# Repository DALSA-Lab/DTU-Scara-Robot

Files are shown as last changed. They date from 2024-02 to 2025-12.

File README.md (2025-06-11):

# Bioscara - DALSA DIY SCARA robot arm
This repository serves to collect all information regarding DTU DALSAs DIY robot arm Bioscara version 2.
Version 2 is defined by replacing the MKS SERVO42C stepper drivers with the Ustepper S32 drivers and removing the 3D printer board. The orignal repository can be found in the bioscara_v1 branch.

## Documentation
The documentation for the joint communication interface can be found in [/docs](/docs/). The documentation is made with Doxygen, its configuration file is in the root of the folder. The documentation can be found as a pdf [/docs/latex/refman.pdf](/docs/latex/refman.pdf) and as html in [/docs/html/index.html](/docs/html/index.html)

## Usage
The robots controller is a Raspberry Pi 4. The RPI is configured to connect to a WIFI network with the the following credentials:  
**SSID**: DALSA_IOT  
**Password**: dalsa_iot  
The easiest way to establish the network is to create a WIFI hotspot with the above credentials, however static IP assignemnt is not possible using Windows Hotspot, and hence the IP address must be checked before any connection attempt.
On the RPI remote login and remote desktop as well as SSH is activated. This way the desktop can be accessed through a RDP software like Windows Remote Desktop or Remina. Be carefull that connecting this way will create a new user session!

Interacting with the robot is handled through ROS2. In the subdirectory a seperate README can be found explaining how to use the hardware.

## TODO
### Mechanical
- [ ]  Update the Fusion model to with all new parts.
- [x] combine old and new stp and stl files
- [ ] Fix J3 Pulley slipping by increasing surface roughness
- [ ] Gripper Redesign
### Software
- [ ] Finish the TODO list for the Joint Communication Protocol (see the documentation)
- [ ] Create URDF file
- [ ] Get started with MoveIt
### Documentation
- [ ] Continue this TODO list and Readme
- [ ] Improve User guide with detailed descriptions and up to date 3D models
- [ ] Document mechanical changes
- [ ] Document Ubuntu install and configurations
- [ ] Document ROS installation
- [ ] Explain the scripts

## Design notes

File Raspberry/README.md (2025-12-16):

# Setup on the Raspberry Pi
> [!CAUTION]
>
> This list is under development and not complete (yet)

- Install Ubuntu Server 24.04 LTS
- Install openssh-server
- Run the scripts provided in [/scripts](scripts)

## Creating the boot image
Using the latest version of the [Raspberry Pi imager](https://www.raspberrypi.com/software/), flash an SD card (16GB, Class 10) with Ubuntu 24.04 LTS Server.
> [!IMPORTANT]
>
> Since the HDMI ports of the Raspberry Pi are no longer accessible when installed inside the robot, follow the next steps to configure remote access.
> Otherwise you would not even be able to see the shell of the OS.

Flash the SD card with the boot image, you dont need to set custom settings, this will be done in the next step.

When the flashing is finished, copy the [*network-config*](network-config) and [*user-data*](user-data) files to the boot/ partition of the SC card. The *network config* contains the initial netplan configuration. Setting the renderer to NetworkManager sets the WiFi managed by the NetworkManager and hence tools like the nmcli can be used. This file will only be read once per instance (during the first boot). The contents of *network-config* will be copied to */etc/netplan/50-cloud-init.yaml* [Link](https://docs.cloud-init.io/en/latest/reference/network-config-format-v2.html#netplan-passthrough).

The netplan contains the following configutation:
- Sets the Netplan renderer (the backend for which Netplan is creating the configuration files) to NetworkManager.
  - **NOTE**: For unknown reasons while testing theses instructions it has happened that the Pi was not connecting to the AP nor ethernet (and the credentials were 100%). Logging into the Pi with a screen attached showed that the NetworkManager was not installed on the system, this should not happen on a clean installation. If that should happed try one of the following:
    - Create a new boot SD card, but edit *network-config* to use 'networkd' (the systemd-networkd network service) instead of 'NetworkManager' as the Netplan rendered. The when booted up and connected to a network install the NetworkManager (`sudo apt install network-manager`). Edit */etc/netplan/50-cloud-init.yaml* back to 'NetworkManager' as renderer and apply `sudo netplan apply`. The network should now be up and managed by the NetworkManager, not systemd-networkd.
    - Instead of creating a new boot image, connect to the Pi's shell by attaching display and keyboard and change the renderer to 'networkd', apply 'sudo netplan apply', wait for connection `sudo netplan status -a`, then continue as described above with downloading the NetworkManager.
- Wifi:
  - Saves an AP with the SSID: 'DALSA_IOT' and pre-shared key: 'dalsa_iot'
  - This AP should be used as a fallback: The raspberry pi will try to connect to this AP if no other is available. You can then gain access to the Pi by creating an AP with the SSID and PSK with a router/laptop hotspot/phone hotspot. All methods should display the IP adrress of the Pi when it is connected.
- Ethernet:
  - Configures static routing for the eth0 interface for a LAN. Refer to the [Network Configuration](#network-configuration) diagram below.
  - The static IP of the robot (the Raspberry Pi) is set to 10.10.10.2.
  - The ethernet route gets assigned a higher metric to route internet traffic through the wifi interface if it is connected, since the LAN has not internet access.

The *user-data* file contains mostly configuration for the user *scara* with the password 'dtubio'. The ubuntu cloud-init program manages these configurations during instance deployment. Many settings can be set here, the README for reference:
>The user-data of the cloud-init seed. This can be used to customize numerous
aspects of the system upon first boot, from the default user, the default
password, whether or not SSH permits password authentication, import of SSH
keys, the keyboard layout, the system hostname, package installation, creation
of arbitrary files, etc. Numerous examples are included (mostly commented) in
the default user-data.
The format of this file is YAML, and is documented at:
https://cloudinit.readthedocs.io/en/latest/topics/modules.html
https://cloudinit.readthedocs.io/en/latest/topics/examples.html

## Network Configuration
The network architecure is as follows:
```mermaid
graph TD;
subgraph Wifi["Wifi"];

laptop["Laptop
hostname: -"]

DTUsecure["DTUsecure

hostname: -"]:::wifi

laptop<-."IP: 10.209.X.X".->DTUsecure

end
subgraph LAN["LAN"];

robot["Raspberry Pi 
hostname: scara"];

dev["Dev Machine
hostname: scara-dev"];

Switch<--IP: 10.10.10.3-->dev
Switch<--IP: 10.10.10.2-->robot

end

Switch<--IP: 10.10.10.4-->laptop
dev<-."(optional)
IP: 10.209.X.X".->DTUsecure
robot<-."(optional)
IP: 10.209.X.X".->DTUsecure
dev<-."(optional)
IP: 10.209.X.X".->laptop
robot<-."(optional)
IP: 192.168.137.X".->laptop

classDef wifi stroke:#f00
classDef bar stroke:#0f0
classDef foobar stroke:#00f
```

The Laptop is optional but usefull during development. In case a Windows hotspot is used the IP addresses are 192.168.137.X (Subnetmask 255.255.255.0).

### Static IP assignment
The */etc/netplan/50-cloud-init.yaml* should have the contents as the [*network-config*](network-config) file, the following snippet configrues the static IP address:
```yaml
...
  ethernets:
    eth0:
      addresses:
        - 10.10.10.2/24
      routes:
        - to: default
          via: 10.10.10.1
          metric: 700 # Increase the metric so that a the wifi connection (metric: 600) is prefered for internet traffic
      nameservers:
          addresses:
            - 8.8.8.8
            - 8.8.4.4
...
```
And the following a simple WPA wifi access point:
```yaml
...
  wifis:
    wlan0:
      dhcp4: true
      optional: true
      access-points:
        "<access-point-SSID>":
          password: "<access-point-psk>"
...
```
to apply changes to Netplan execute:
```bash
sudo netplan apply
```
### Connecting to DTUsecure
If the robot should be connected to DTUsecure, for example for a faster connection, run the provided [script](scripts/connect_DTUsecure.sh). DTUsecure uses the WPA-EAP authethication mechanism with your DTU id and DTU password. The script has been made to simplify the setup.
> [!CAUTION]
>
> Due the nature of the OS, your DTU accounts password will be saved in plain text in a netplan file on the system if the connection shall be saved persistently betweeen reboots! Follow the scripts output to see where.

To run the script first make it executable as follows:
```bash
cd ~/bioscara/Raspberry/scripts
sudo chmod +x connect_DTUsecure.sh
```
then the script can be run simply by invoking:
```bash
sudo ./connect_DTUsecure.sh
```
The script adds a connection via nmcli, and asks the user for DTU id and password and if the credentials should be saved.

### Further information about network management
Managing networks on Linux can be confusing, for example if interfaces show up as 'unmanaged' the chances are high that a different network manager has control over the interface. [This](https://wiki.archlinux.org/title/Network_configuration#Network_managers) table gives a good overview which programs might be involved.
Note that Netplan is not mentioned there, since Netplan only takes a standardized configuration file as input and then depending on the renderer creates the configuration for the backend. Currently Netplan only works with systemd-networkd and NetworkManager, the latter is much simpler to use with its CLI `nmcli`, and terminal UI `nmtui`. 

## Realtime Requirements
Both of the following settings were set to the best realtime performance after the installation of Ubuntu Server 24.04 LTS on the Raspberry Pi. This is how to check and change them if necessary.

This set of kernel configuration is also set when installing the "Low Latency Ubuntu" (`sudo apt install linux-lowlatency`)

### Preemption Policy 

In mainline Ubuntu the maximum preemption policy is PREEMPT. Check if set using:
Check if enabled if CONFIG_PREEMPT is set:
```bash
cat /boot/<BUILD?> | grep CONFIG_PREEMPT
```
last \<BUILD\> = config-6.8.0-1028-raspi

> PREEMPT_VOLUNTARY: This config option adds preemption points to the kernel, enabling voluntary interrupts of low-priority processes. By providing faster application responses with only slightly reduced throughput, CONFIG_PREEMPT_VOLUNTARY suits desktop environments.
>
> PREEMPT: Enabling CONFIG_PREEMPT reduces the kernel latency by making low-priority processes involuntarily preempt themselves. Preemption is disabled only at critical locations where the kernel must protect data from concurrency. Such config option fits embedded applications with latency requirements in the order of milliseconds. [source](https://ubuntu.com/blog/industrial-embedded-systems-ii)

### Interrupt Timer Resolution
> The timer interrupt handler interrupts the kernel at a rate set by the HZ constant. The frequency affects the timer resolutions as a 100 Hz value for the timer granularity will yield a max resolution of 10ms (1 Hz equating to 1000ms), 250Hz will result in 4ms, and 1000Hz in the best-case resolution of 1ms. [source](https://ubuntu.com/blog/industrial-embedded-systems-ii)

```bash
cat /boot/<BUILD?> | grep CONFIG_HZ
```
last \<BUILD\> = config-6.8.0-1028-raspi

### Adding the scara user to realtime group
Add the user to the realtime group and give it the rights to set higher scheduler priotities as described [here](https://control.ros.org/jazzy/doc/ros2_control/controller_manager/doc/userdoc.html#determinism)

| For real-time tasks, a priority range of 0 to 99 is expected, with higher numbers indicating higher priority. By default, users do not have permission to set such high priorities. To give the user such permissions, add a group named realtime and add the user controlling your robot to this group:

```bash
sudo addgroup realtime
sudo usermod -a -G realtime $(whoami)
```
| Afterwards, add the following limits to the realtime group in /etc/security/limits.conf:
```
@realtime soft rtprio 99
@realtime soft priority 99
@realtime soft memlock unlimited
@realtime hard rtprio 99
@realtime hard priority 99
@realtime hard memlock unlimited
```
| The limits will be applied after you log out and in again.

## Other Dependencies
The order of managing dependenices is according to [this](https://ros2-quality-assurance.readthedocs.io/en/released/tutorials/dependencies.html) guideline the following:
1. **rosdep**: Installs missing dependecies specified in the packages via the systems package manager.
2. **vcstool**: Specify further source code repositoryies in a repository file, vcstool will then retrieve the repository and it can then be built with colcon. 
3. **other**

### ROS2 dependencies
To install ROS2 package dependencies navigate to the workspace:
```bash
cd lib/ros2_ws
```

**First:**
Fetch all dependecies that are not available as binaries using the *vcstool*.
From the workspace execute:
```bash
vcs import --recursive src < req.repos
```
This will pull the repositories specified in *req.repos* into the directories also specified in the file.

> [!NOTE]
>
> *vcstool* is found in many ROS2 packages to import dependencies that are not in a ROS or debian repository from a repository file. 
>
> **Installation**:
>
> ```bash
> sudo apt install python3-vcstool
> ```

**Second:**

Install all packages that can be resolved through `rosdep` (all packages that have been released to the ROS2 package ecosystem and some debian packages):
```bash
sudo apt update
rosdep install --from-paths src --ignore-src -y --rosdistro $ROS_DISTRO
```
This command will recursively scan every package in the workspace for the `<depend/>` key and install missing packages.

Then dont forget to build the workspace:
```bash
sudo apt remove ros-$ROS_DISTRO-moveit*
rm -rf build/ install/ log/
MAKEFLAGS="-j1 -l1" colcon build --mixin release --executor sequential --symlink-install > log.out &
```

## Development Purposes:
### Install [PlotJuggler](https://github.com/facontidavide/PlotJuggler)
A very powerfull tool to to display data
```bash
sudo apt install ros-$ROS_DISTRO-plotjuggler-ros
```

### Install RQT tools
```bash
sudo apt install ros-jazzy-rqt*
```

### For debugging
```bash
sudo apt install xterm gdb gdbserver
```

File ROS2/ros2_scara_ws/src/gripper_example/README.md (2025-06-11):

# Robot Gripper  
The gripper is driven by a PWM controlled RC servo. The frequency is 50 Hz. The PWM should be a hardware generated PWM as software PWM has potentiall hight jitter which could cause overheating.
Interacting with the gripper is done through the Gripper class defined in joint_communication/mGripper.h. See the relevant documentation also in the HTML or PDF documentation of the joint_communication protocol.  

## Usage
First build the package with Colcon, then you can run it after it is sourced.
### Building
```bash
cd ~/bioscara/ROS2/ros2_scara_ws
colcon build --packages-select gripper_example
```
### Running
In a new terminal:
```bash
cd ~/bioscara/ROS2/ros2_scara_ws
source install/local_setup.sh
ros2 run gripper_example main 
 ```

Sourcing only is necessary once after opening a new terminal.

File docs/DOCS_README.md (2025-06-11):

# Documentation
This documentation currently documents how the robot controller communicates with the joint controllers, this includes:
- The joint firmware in the [/Arduino](../Arduino/) directory
- The interfacing library used for communicating with the joints in the [/ROS2](../ROS2/ros2_scara_ws/src/joint_communication/) directory.

# Usage
the joint_communication library is structured as a ROS2 package but can also be used in another build toolchain. If that is the case ensure the include paths are still correct.

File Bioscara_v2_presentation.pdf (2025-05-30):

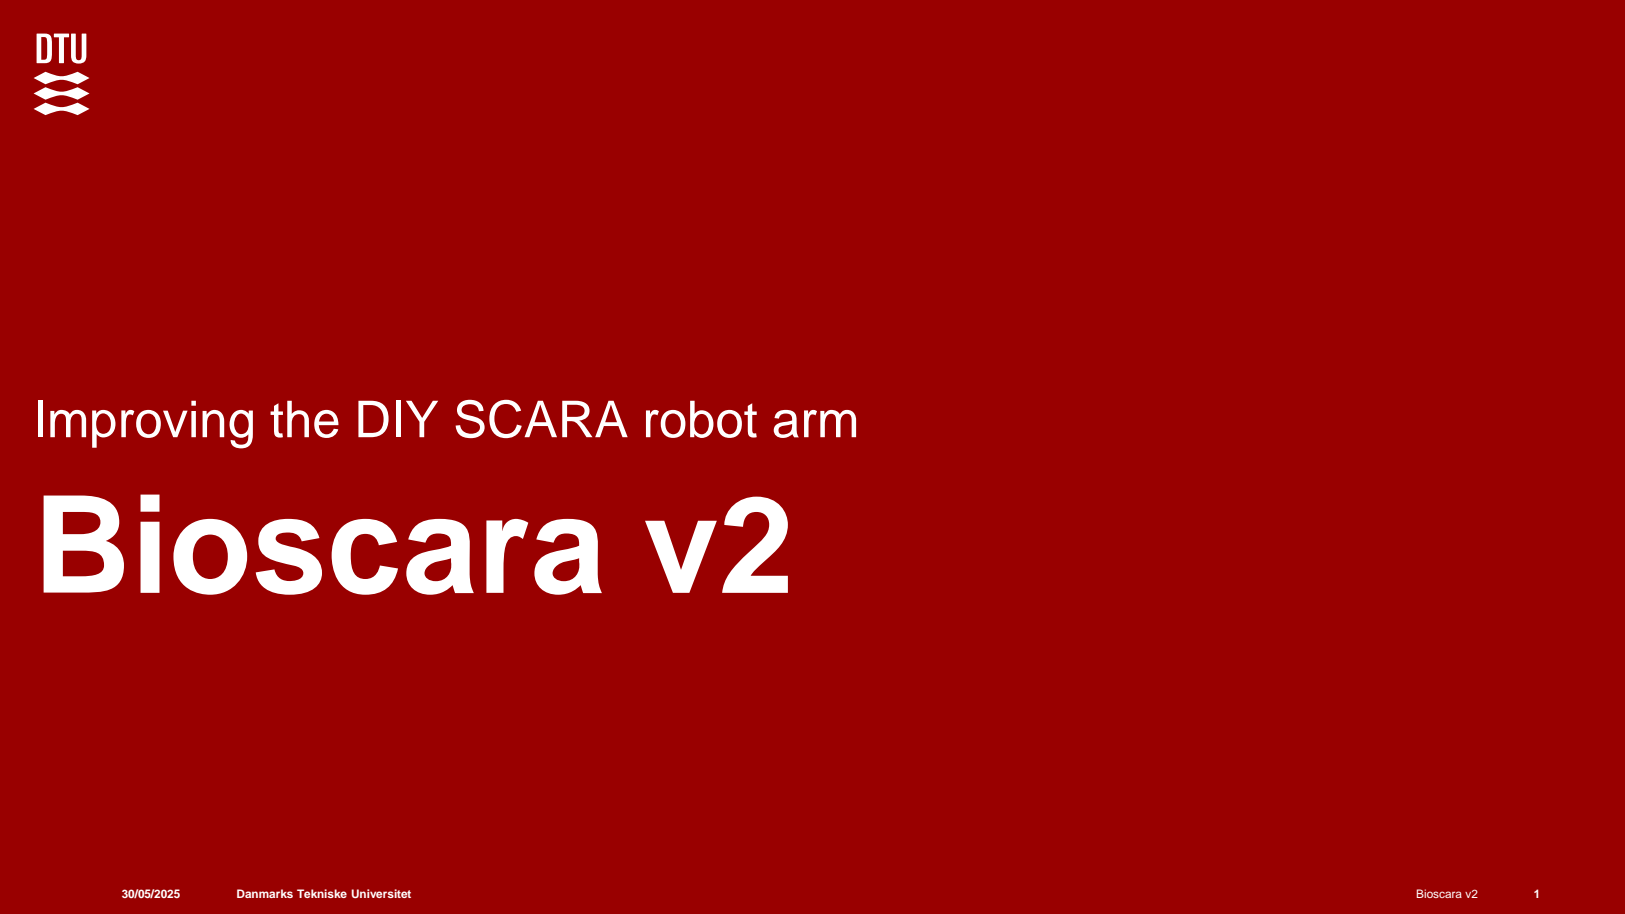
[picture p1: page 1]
Bioscara v2

Improving the DIY SCARA robot arm
Bioscara v2

Danmarks Tekniske Universitet

# Aim

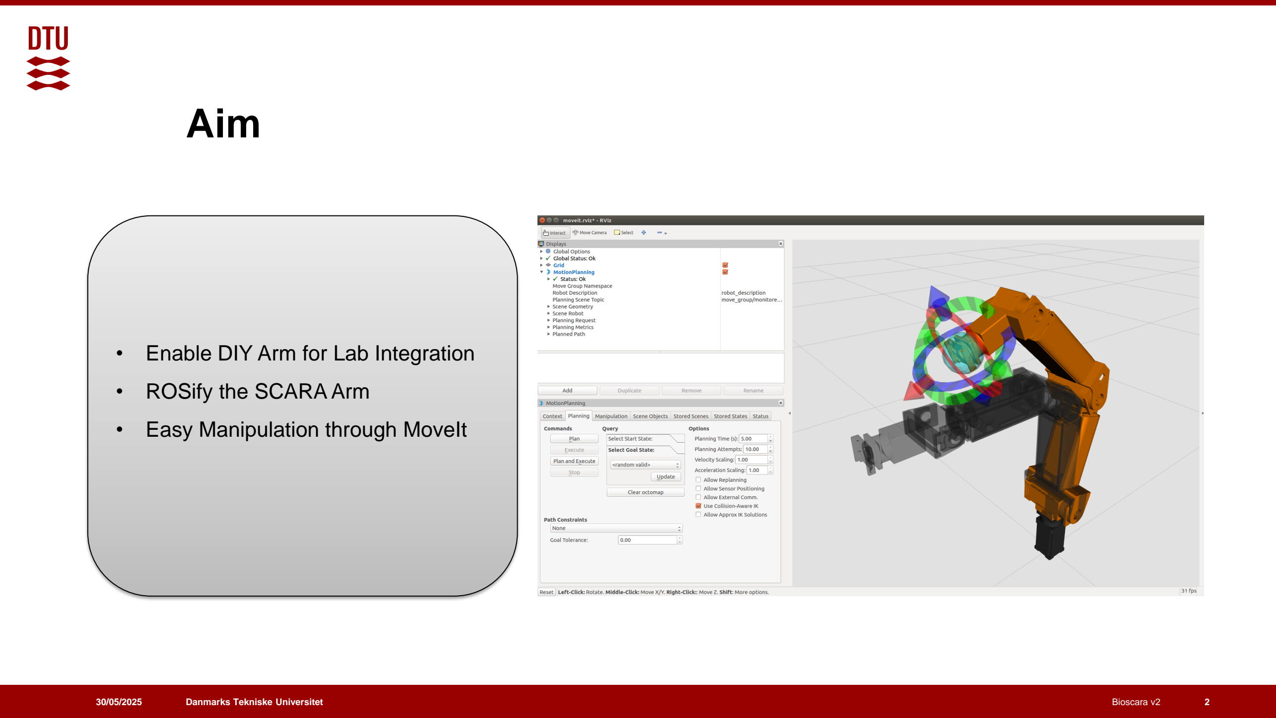
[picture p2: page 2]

30/05/2025 | Bioscara v2 | 2
- Enable DIY Arm for Lab Integration
- ROSify the SCARA Arm
- Easy Manipulation through MoveIt

# Automation Pipeline

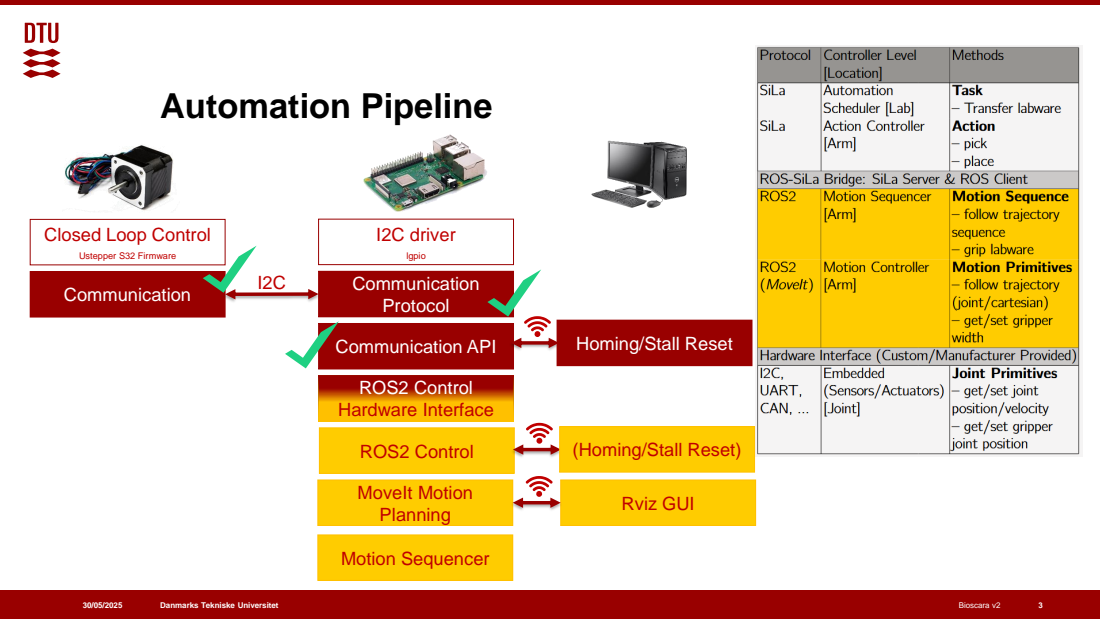
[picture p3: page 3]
Bioscara v2; Ustepper S32 Firmware; Communication; I2C driver; lgpio Communication Protocol; Communication API; ROS2 Control Hardware Interface; ROS2 Control; MoveIt Motion Planning; Rviz GUI; Motion Sequencer

Closed Loop Control

Homing/Stall Reset

(Homing/Stall Reset)

# Architecture (old)

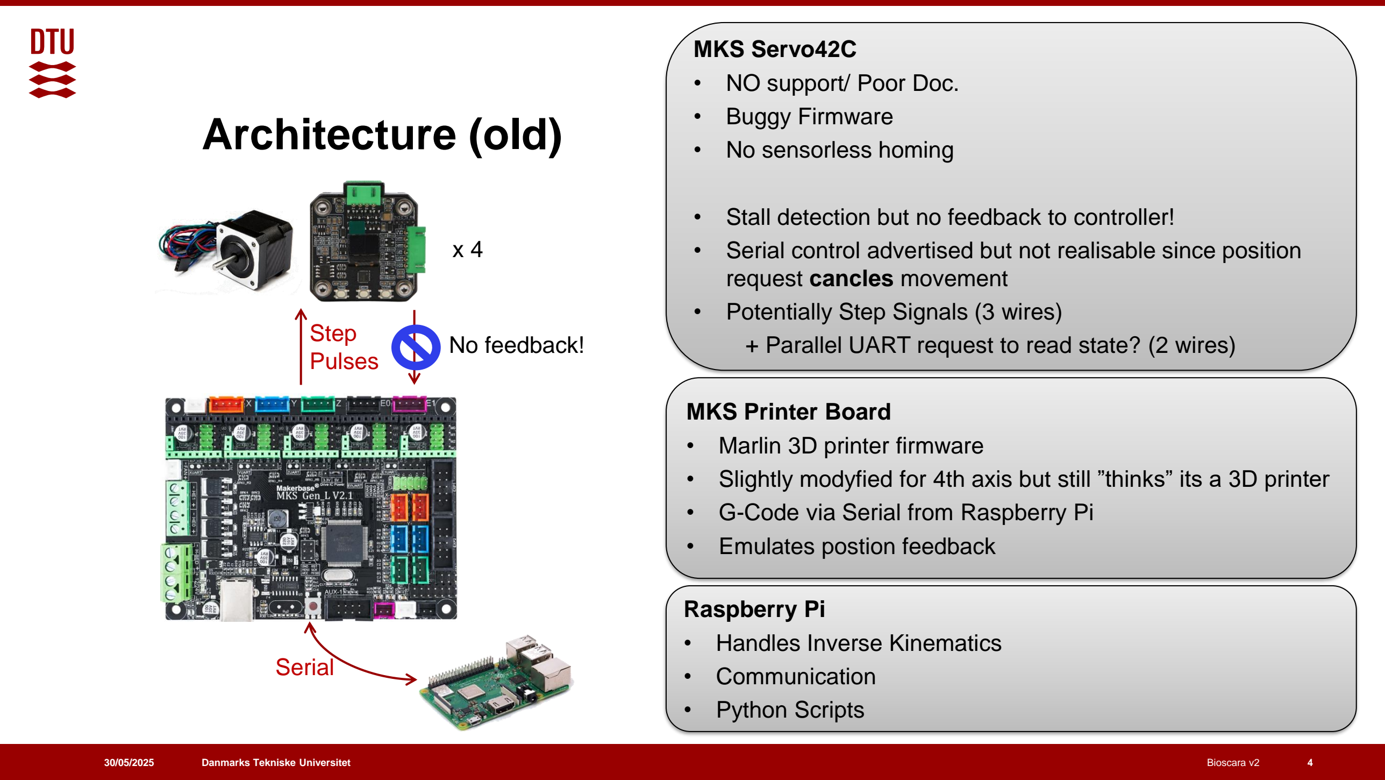
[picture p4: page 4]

30/05/2025 | Bioscara v2 | 4

Step
Pulses | No feedback!

MKS Servo42C
- NO support/ Poor Doc.
- Buggy Firmware
- No sensorless homing
- Stall detection but no feedback to controller!
- Serial control advertised but not realisable since position request cancles movement
- Potentially Step Signals (3 wires)
+ Parallel UART request to read state? (2 wires)

Serial

MKS Printer Board
- Marlin 3D printer firmware
- Slightly modyfied for 4th axis but still ”thinks” its a 3D printer
- G-Code via Serial from Raspberry Pi
- Emulates postion feedback

Raspberry Pi
- Handles Inverse Kinematics
- Communication
- Python Scripts

x 4

# Old Schematic

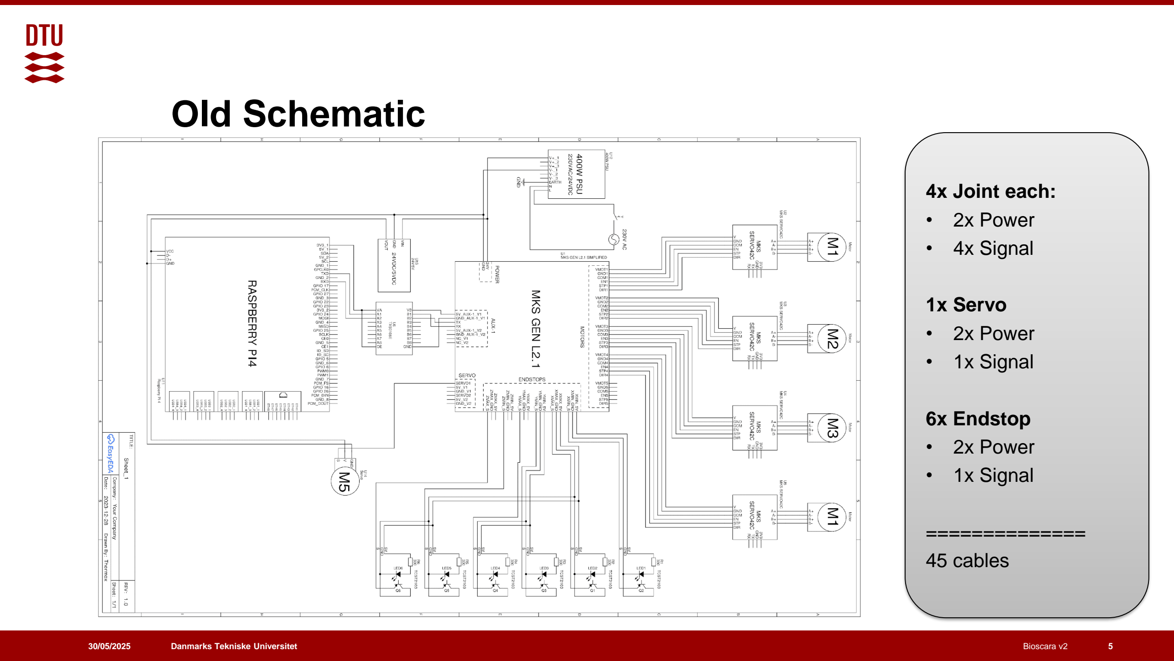
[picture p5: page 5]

30/05/2025 | Bioscara v2 | 5

4x Joint each:
- 2x Power
- 4x Signal

1x Servo
- 2x Power
- 1x Signal

6x Endstop
- 2x Power
- 1x Signal

==============
45 cables

# Architecture (new)

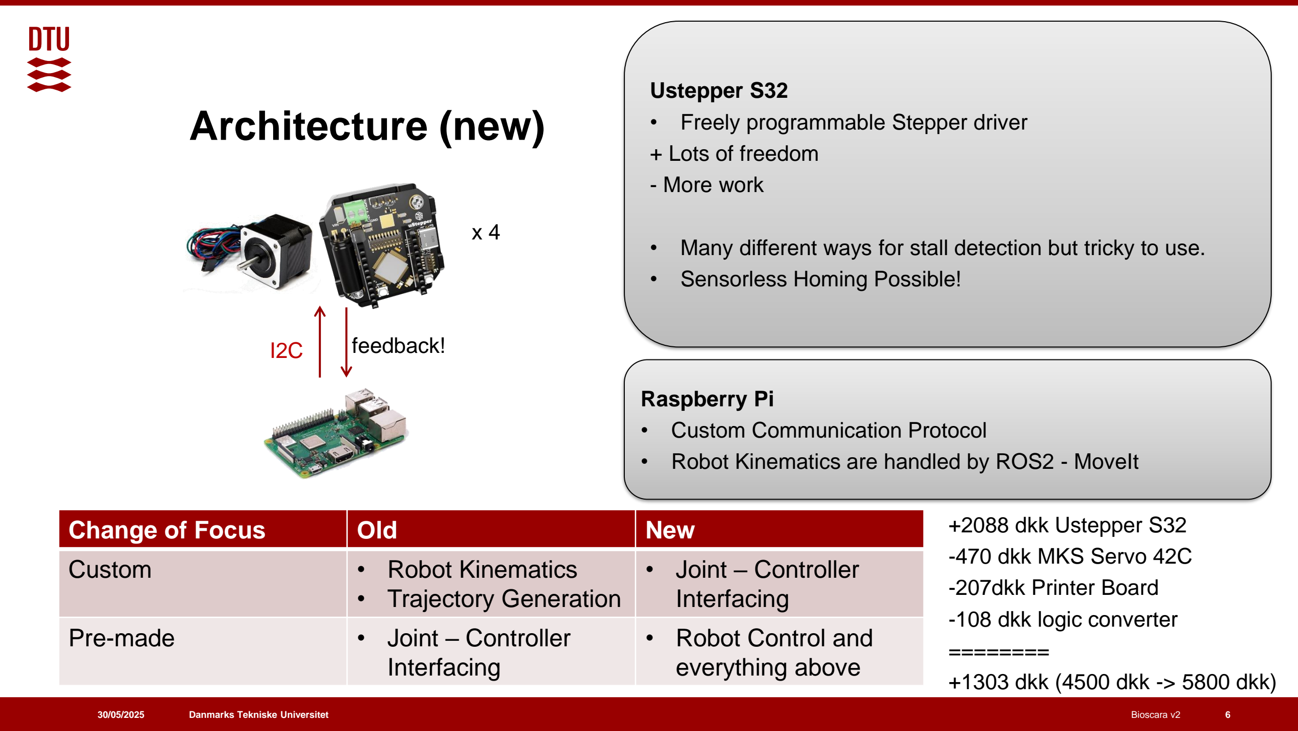
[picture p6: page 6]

30/05/2025 | Bioscara v2 | 6

Ustepper S32
- Freely programmable Stepper driver + Lots of freedom
- More work
- Many different ways for stall detection but tricky to use.
- Sensorless Homing Possible!

Raspberry Pi
- Custom Communication Protocol
- Robot Kinematics are handled by ROS2 - MoveIt
I2C | feedback!
Change of Focus | Old | New
Custom | • Robot Kinematics • Trajectory Generation | • Joint – Controller Interfacing
Pre-made | • Joint – Controller Interfacing | • Robot Control and everything above

+2088 dkk Ustepper S32
-470 dkk MKS Servo 42C
-207dkk Printer Board
-108 dkk logic converter
========
+1303 dkk (4500 dkk -> 5800 dkk)

x 4

# Sensorless Homing

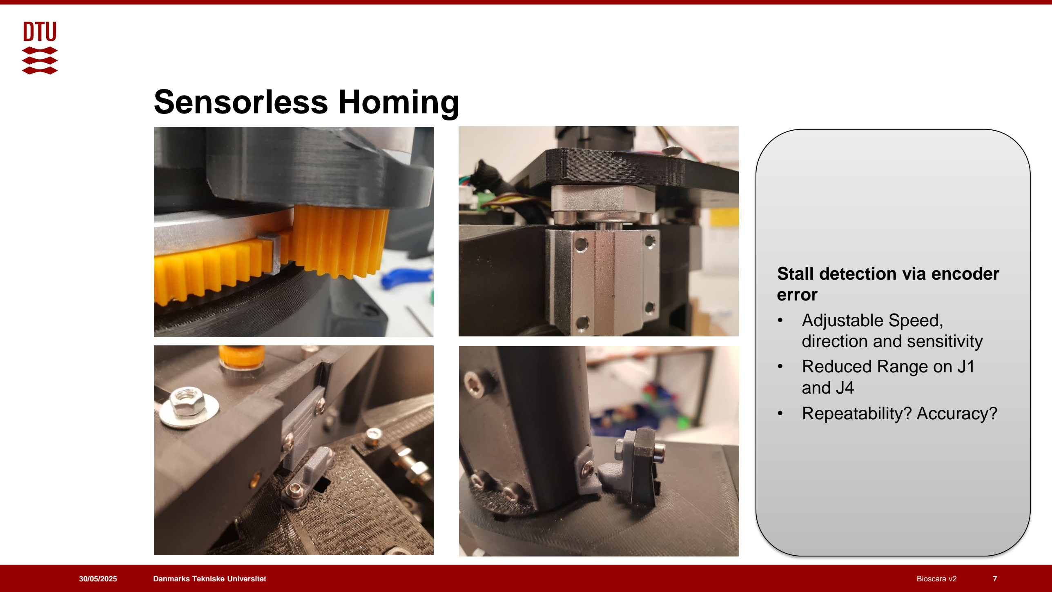
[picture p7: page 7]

30/05/2025 | Bioscara v2 | 7

Stall detection via encoder error
- Adjustable Speed,
direction and sensitivity
- Reduced Range on J1
and J4
- Repeatability? Accuracy?

# Videos

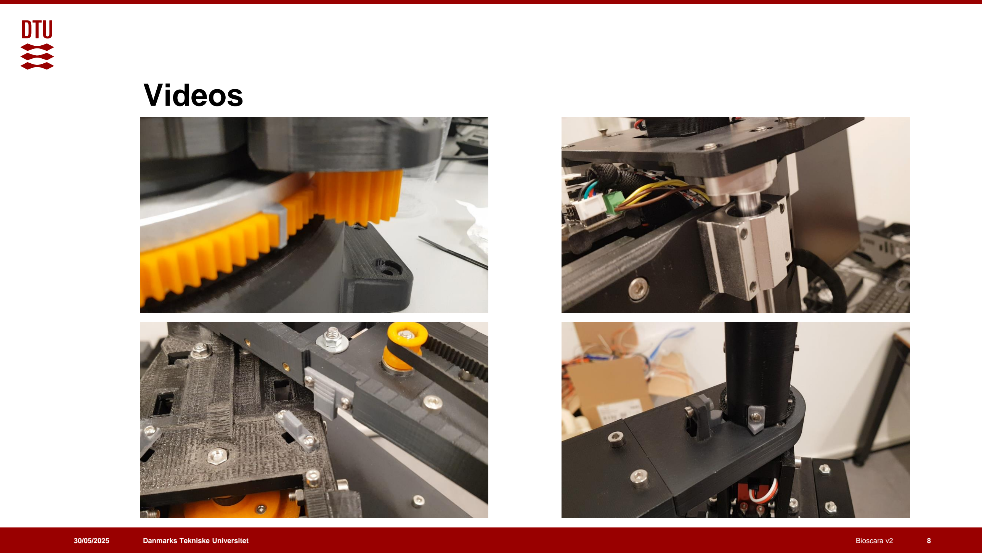
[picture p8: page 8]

30/05/2025 | Bioscara v2 | 8

# New Schematic

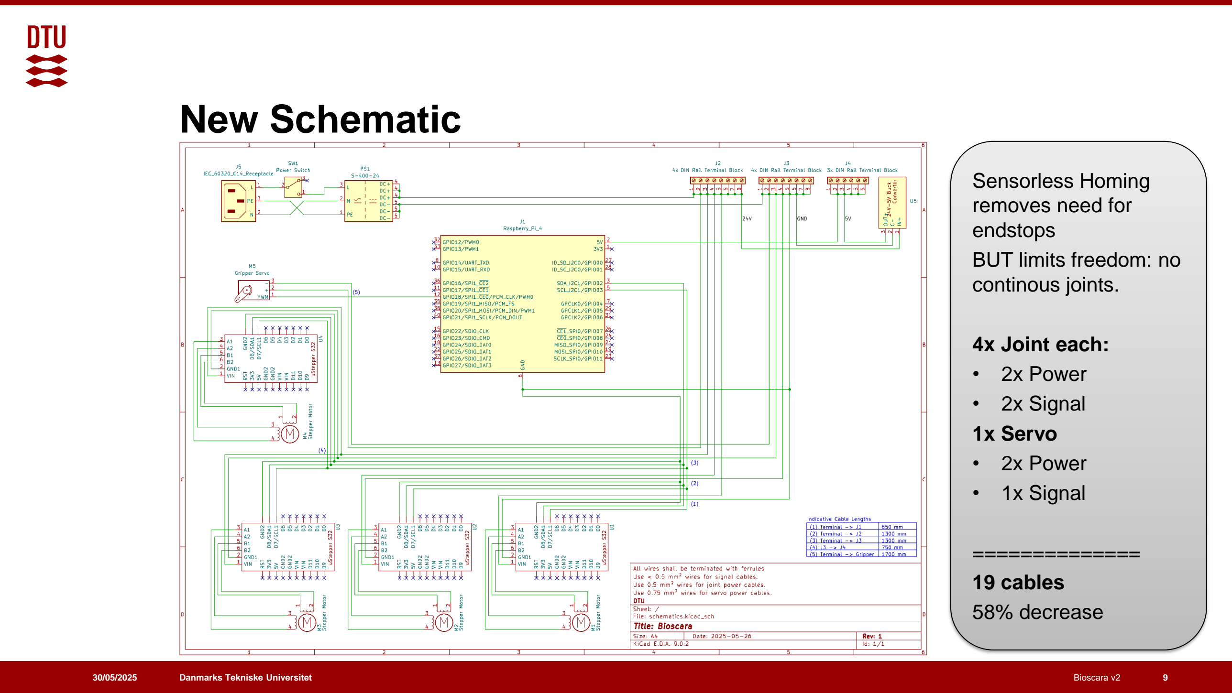
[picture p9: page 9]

30/05/2025 | Bioscara v2 | 9

Sensorless Homing
removes need for
endstops
BUT limits freedom: no
continous joints.

4x Joint each:
- 2x Power
- 2x Signal
1x Servo
- 2x Power
- 1x Signal

==============

### 19 cables

58% decrease

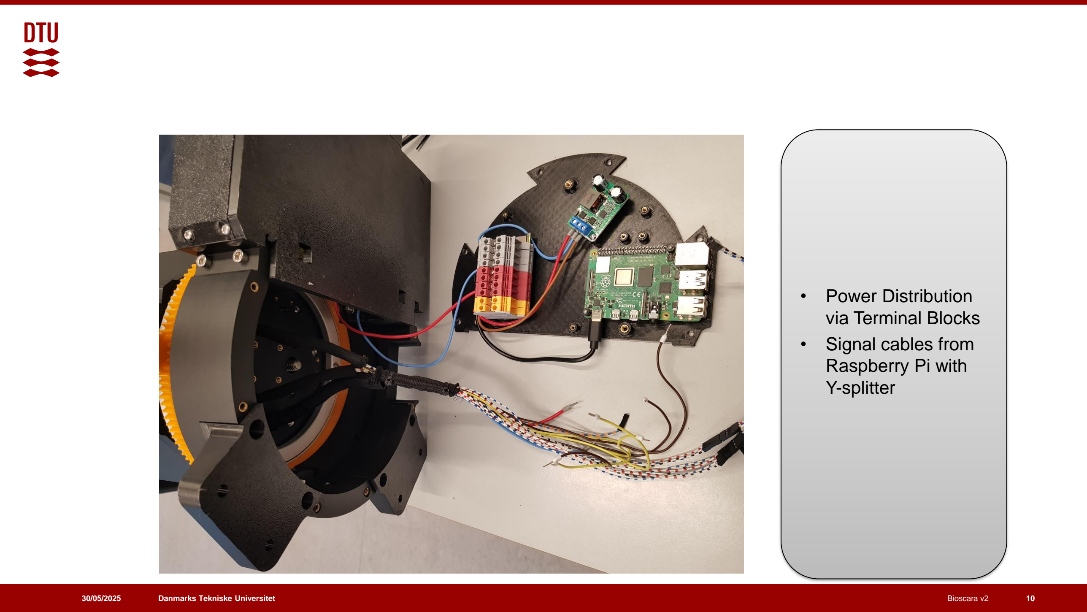
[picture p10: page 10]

30/05/2025 | Danmarks Tekniske Universitet | Bioscara v2 | 10
- Power Distribution
via Terminal Blocks
- Signal cables from
Raspberry Pi with
Y-splitter

# Code Dependencies and Documentation

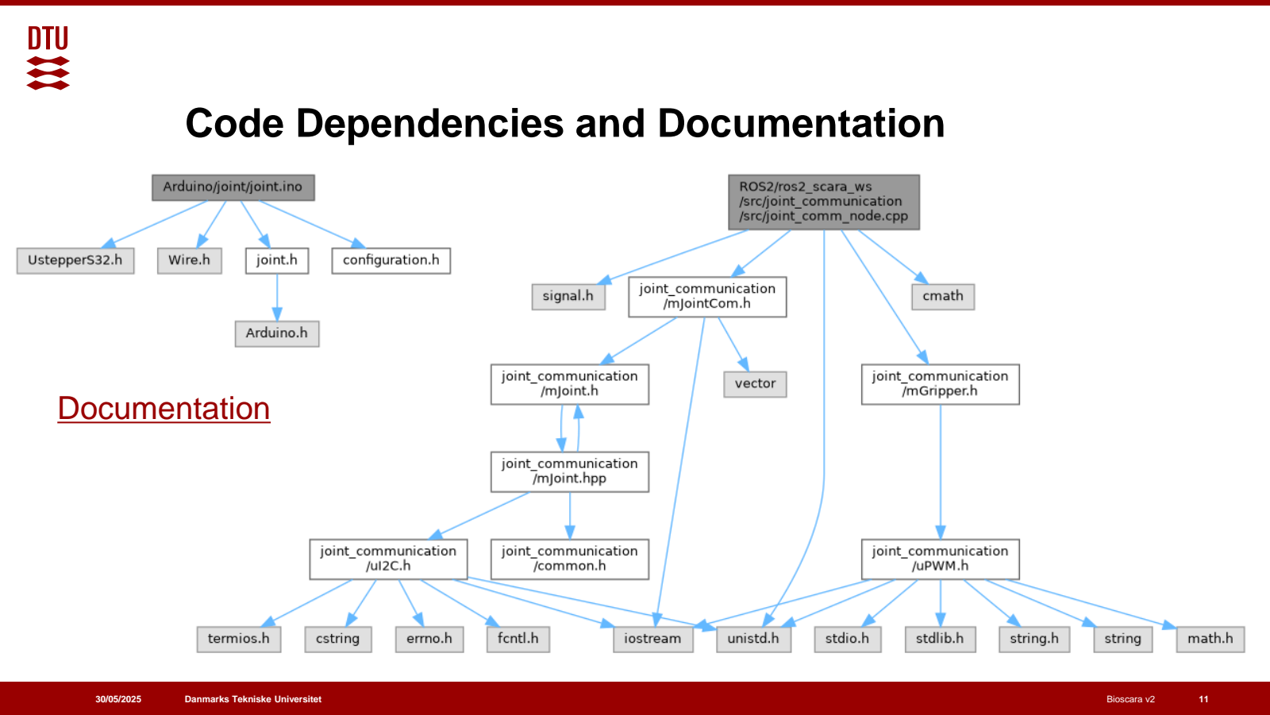
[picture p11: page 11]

30/05/2025 | Bioscara v2 | 11

## Documentation

# Joint Communication Protocol

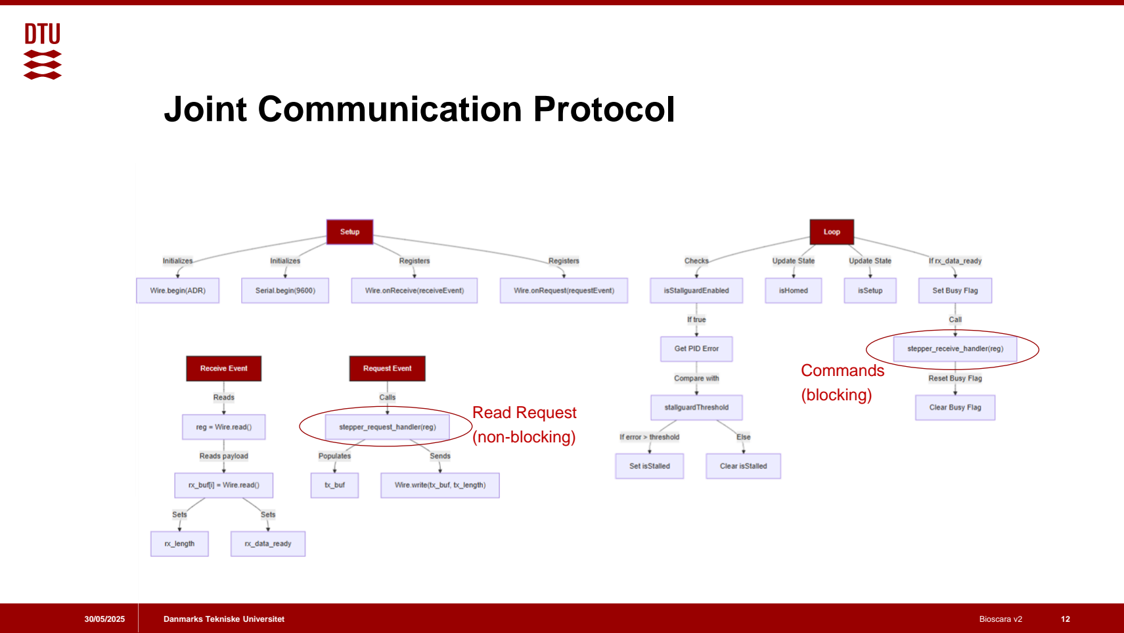
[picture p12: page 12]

30/05/2025 | Bioscara v2 | 12

Read Request
(non-blocking)

Commands
(blocking)

# Buy Cheap, buy twice

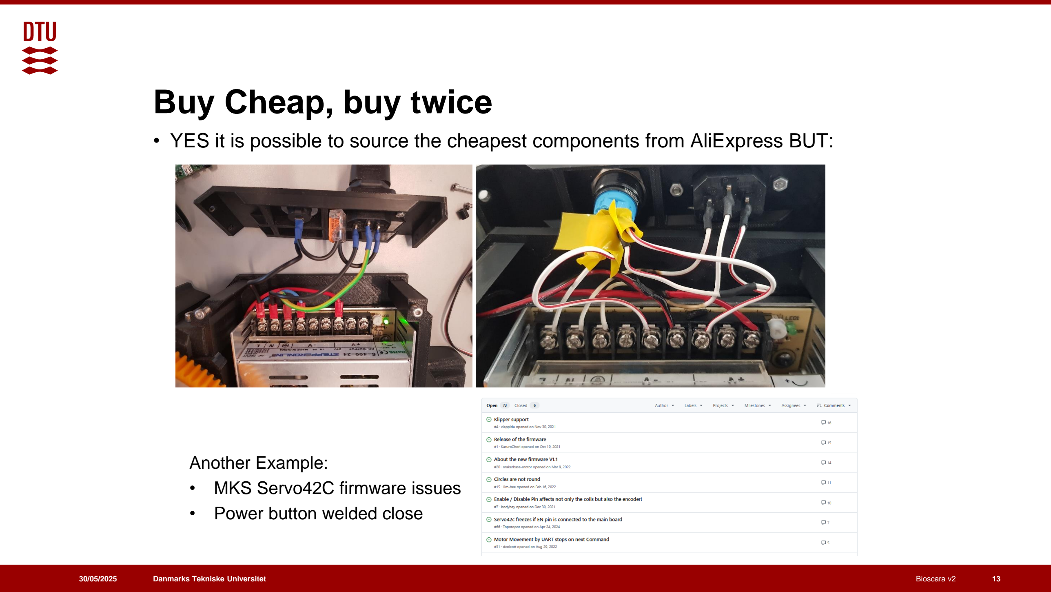
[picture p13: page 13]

- YES it is possible to source the cheapest components from AliExpress BUT:
30/05/2025 | Bioscara v2 | 13

Another Example:
- MKS Servo42C firmware issues
- Power button welded close

# TODO

- Mechanical:
– J3 lower arm to newest version
– J3 tension pulley slip:
- Fix with set screw or similar
- Increase friction by roughing surface
– Gripper redesign with sufficient clearance
- Test Accuracy and Precision of sensorless homing
- Test Robustness of Communication Protocol
- Homing Script (through ROS or as plain script)
- For motion with MoveIt:
– Create ROS2 Control Hardware Interface – Create URDF description file
– Adapt simple example
30/05/2025 | Bioscara v2 | 14

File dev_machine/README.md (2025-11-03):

# Setup on the Dev machine
- Install openssh-server
        ```bash
    sudo apt install openssh-server
    ```
- enable ssh on boot
    ```bash
    sudo systemctl enable ssh
    ```
- install net-tools

## install ROS2
using this [script](scripts/ROS2-Jazzy_install.sh) with arguments domain ID = 41 and version ROS-Desktop

## Install ROS2_control
Although not neccessarily needed, this package comes with some handy tools that might be usefull.
```bash
sudo apt install ros-$ROS_DISTRO-ros2-control ros-$ROS_DISTRO-ros2-controllers
```

In my case xacro was not installed, had to manually install it using
```bash
sudo apt install ros-$ROS_DISTRO-xacro
```

## Network Configuration
The dev-machine is connected to the robot via a local private network via a switch like displayed [here](../Raspberry/README.md#network-configuration).

### Assign a static IP
create the */etc/netplan/99_config.yaml* file with following content:
```yaml
network:
  version: 2
  renderer: networkd
  ethernets:
    eno1:
      addresses:
        - 10.10.10.3/24
      routes:
        - to: default
          via: 10.10.10.1
          metric: 700 # Increase the metric so that a the wifi connection (metric: 600) is preffered for internet traffic
      nameservers:
          addresses:
            - 8.8.8.8
            - 8.8.4.4
```
to apply the changes execute:
```bash
sudo netplan apply
```

### Create a static hostname entry
in the */etc/hosts* add the following line:
```
10.10.10.3 scara-dev
```

## Development Purposes:
### Install [PlotJuggler](https://github.com/facontidavide/PlotJuggler)
A very powerfull to to display data
```bash
sudo snap install plotjuggler
```

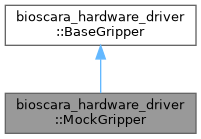
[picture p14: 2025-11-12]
docs/html/classbioscara__hardware__driver_1_1MockGripper__inherit__graph.png

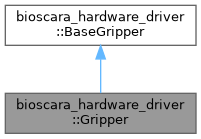
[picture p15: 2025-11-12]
docs/html/classbioscara__hardware__driver_1_1Gripper__inherit__graph.png

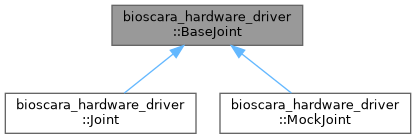
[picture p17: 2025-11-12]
docs/html/classbioscara__hardware__driver_1_1BaseJoint__inherit__graph.png

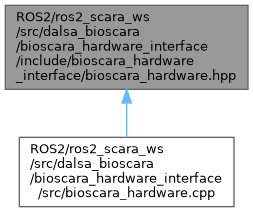
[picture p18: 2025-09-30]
docs/html/bioscara__hardware_8hpp__dep__incl.png

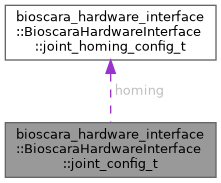
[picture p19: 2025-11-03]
docs/html/structbioscara__hardware__interface_1_1BioscaraHardwareInterface_1_1joint__config__t__coll__graph.png

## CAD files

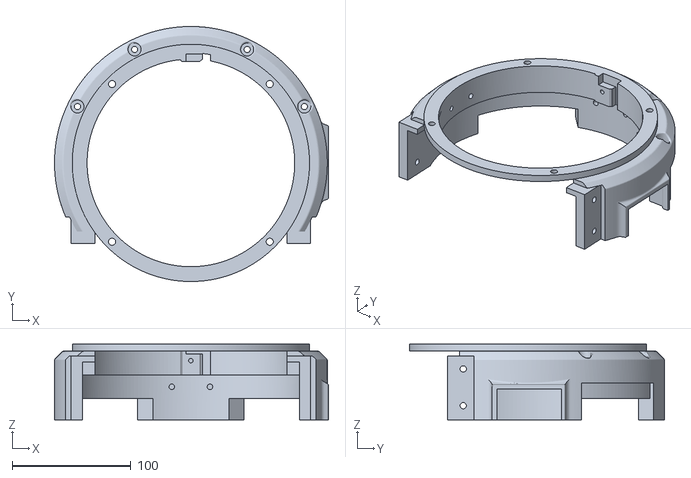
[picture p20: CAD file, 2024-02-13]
Assembly/3D models/Robot base/Robot base main body.stl
231.0 x 215.0 x 64.0

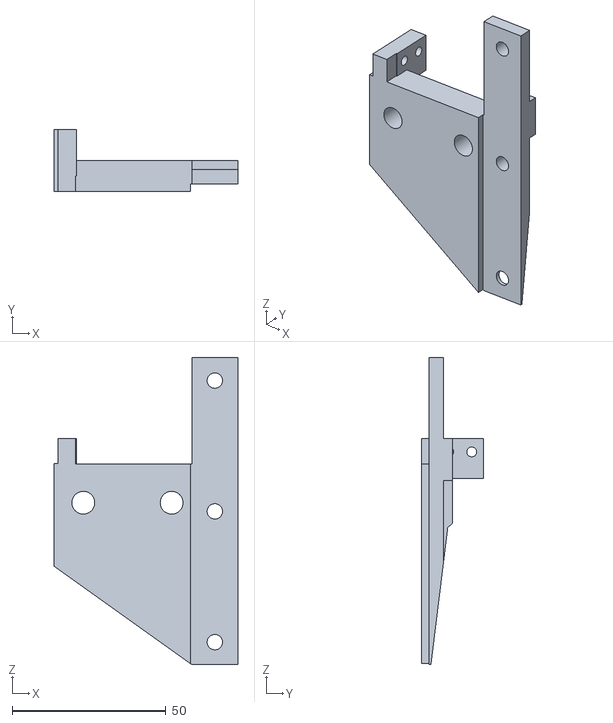
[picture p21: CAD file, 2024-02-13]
Assembly/3D models/Gripper/Left claw mount.stl
59.7 x 20.0 x 99.8

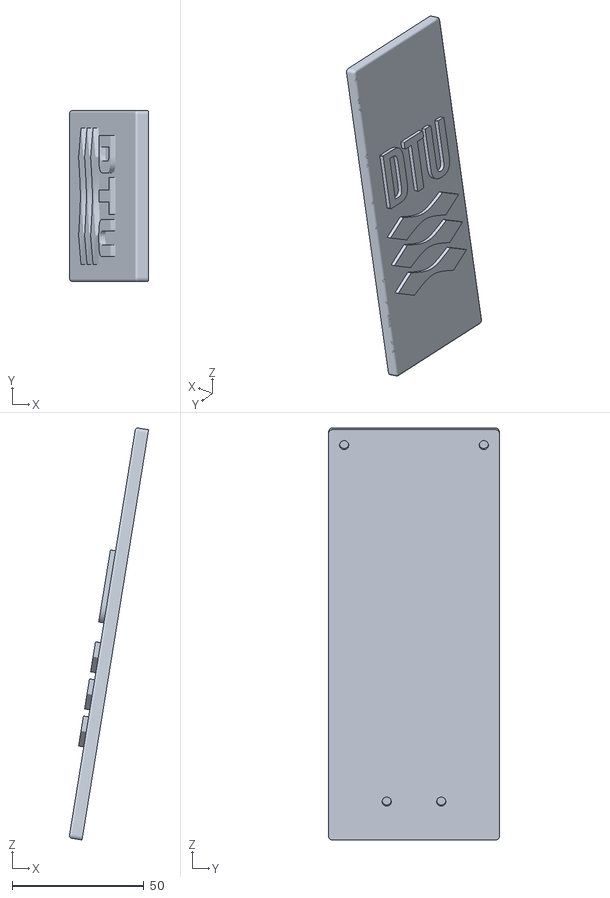
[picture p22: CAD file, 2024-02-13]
Assembly/3D models/Joint 1/DTU logo.stl
30.0 x 64.8 x 156.1

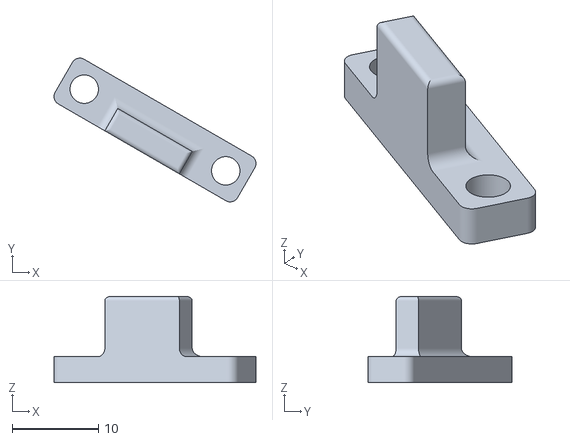
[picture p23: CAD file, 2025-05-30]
Assembly/3D models/Joint 2/J3_endstop_l.stl
23.5 x 16.7 x 10.0

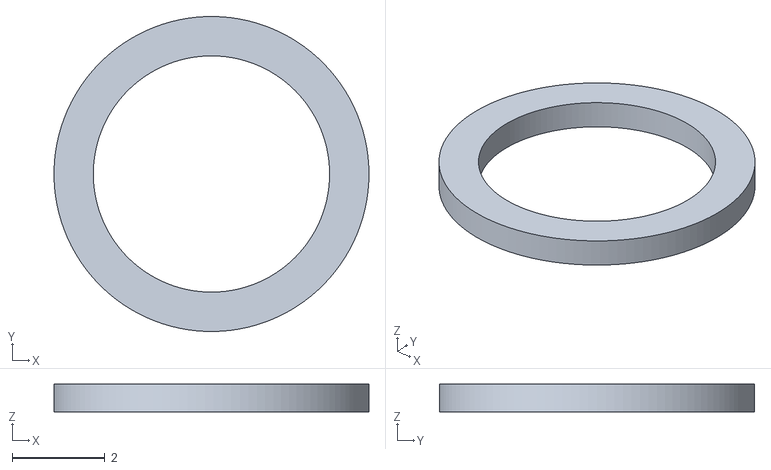
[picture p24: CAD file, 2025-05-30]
Assembly/3D models/Joint 3/Pulley_spacer.stl
6.80 x 6.80 x 0.6

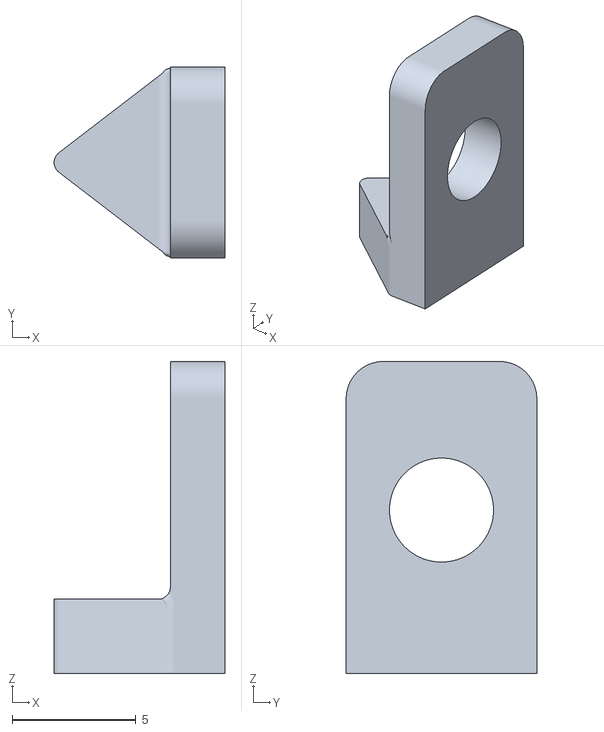
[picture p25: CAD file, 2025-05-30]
Assembly/3D models/Joint 4/J4_Trigger.stl
6.90 x 7.70 x 12.6

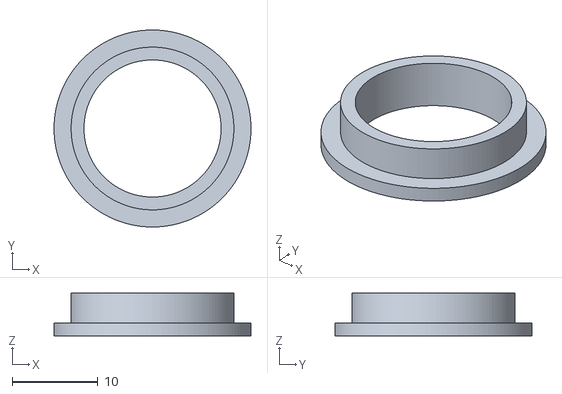
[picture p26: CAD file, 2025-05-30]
Assembly/3D models/Robot base/switch_faceplate_adapter.stl
23.0 x 23.0 x 5.00

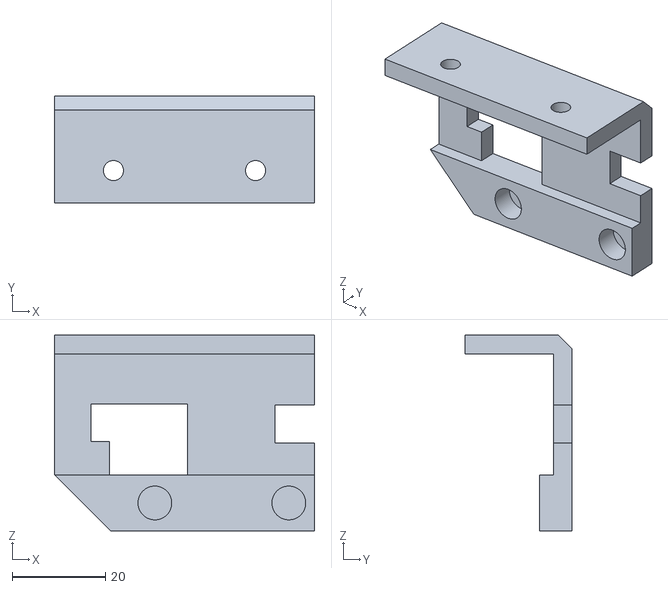
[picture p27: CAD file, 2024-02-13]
Assembly/3D models/Gripper/Left mount.stl
55.7 x 23.0 x 42.0

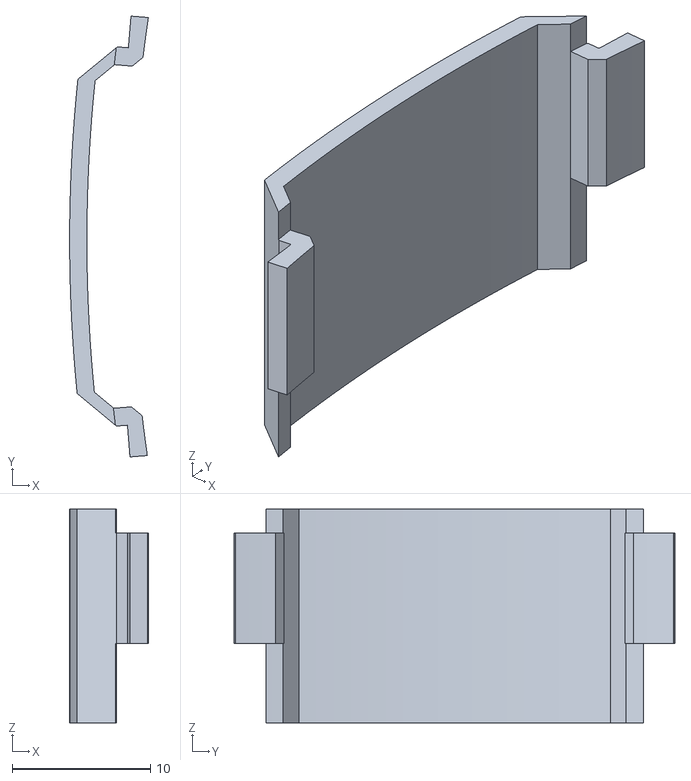
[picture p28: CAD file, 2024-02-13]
Assembly/3D models/Joint 1/Clip 2.stl
5.69 x 31.9 x 15.5

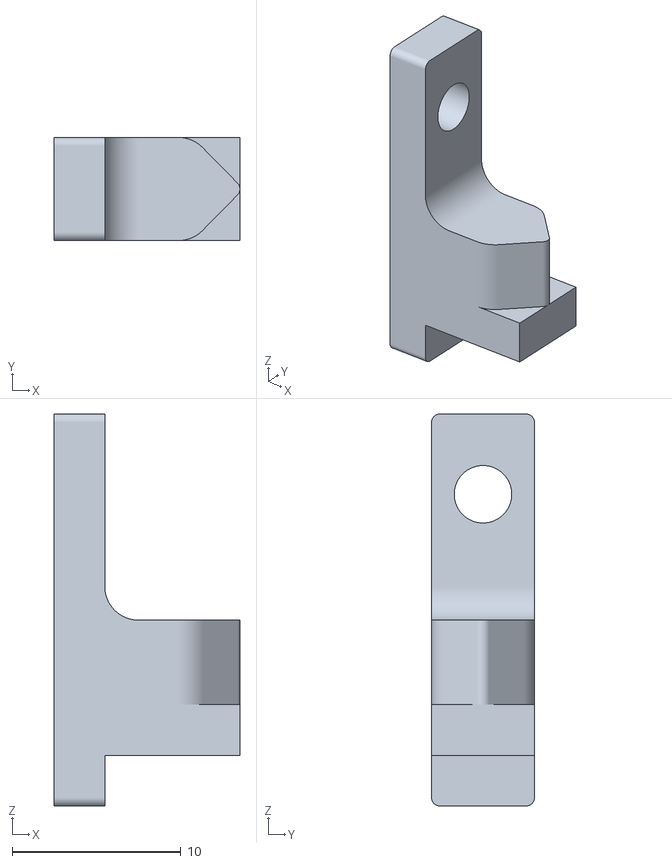
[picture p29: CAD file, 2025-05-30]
Assembly/3D models/Joint 3/J4_endstop.stl
11.0 x 6.10 x 23.2

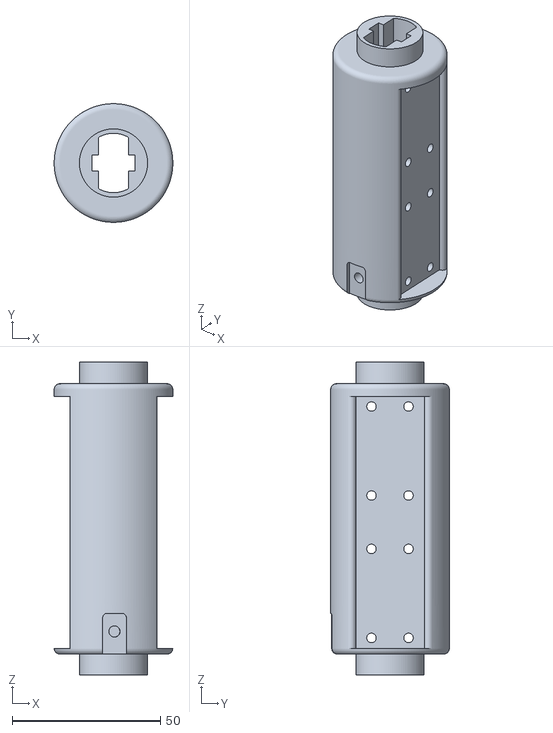
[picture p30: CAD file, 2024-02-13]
Assembly/3D models/Joint 4/J4 roller.stl
40.0 x 40.0 x 105.5

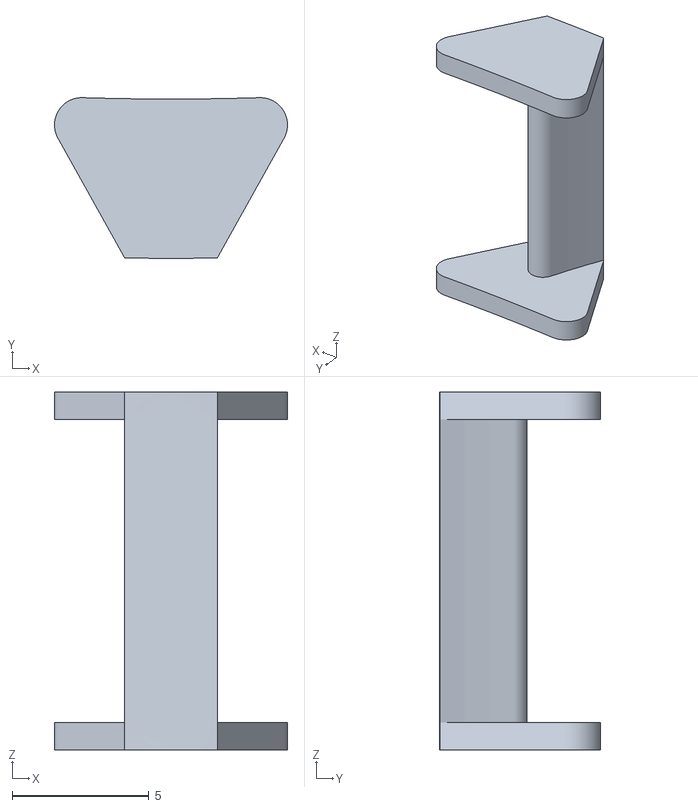
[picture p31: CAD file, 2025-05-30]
Assembly/3D models/Robot base/J1_endstop.stl
8.53 x 5.88 x 13.1

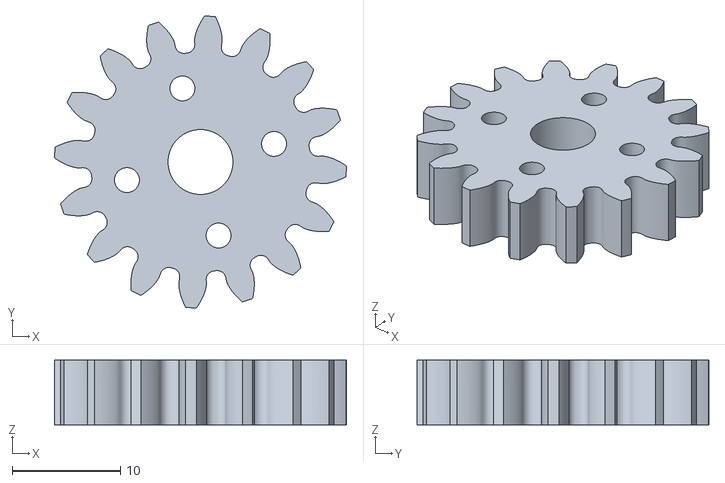
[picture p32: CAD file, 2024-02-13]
Assembly/3D models/Gripper/Spur gear 16T.stl
27.0 x 27.0 x 6.00

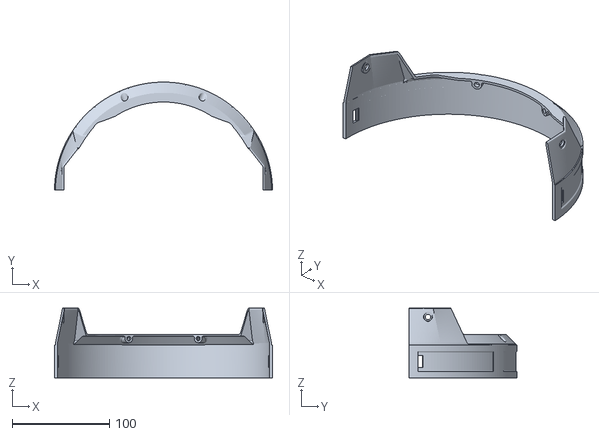
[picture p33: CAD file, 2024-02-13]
Assembly/3D models/Joint 1/Cover 2.stl
224.5 x 111.0 x 72.0

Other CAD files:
Assembly/3D models/Joint 2/J3_endstop_r.stl
Assembly/3D models/Joint 2/J2 cover 2.stl
Assembly/3D models/Joint 3/Cable holder 1.stl
Assembly/3D models/Joint 4/80T gear.stl
Assembly/3D models/Gripper/Gripper base.stl
Assembly/3D models/Gripper/Left gripper mount.stl
Assembly/3D models/Gripper/Left rack gear.stl
Assembly/3D models/Gripper/Right claw mount.stl
Assembly/3D models/Gripper/Right gripper mount.stl
Assembly/3D models/Gripper/Right mount.stl
Assembly/3D models/Gripper/Right rack gear.stl
Assembly/3D models/Joint 1/Base.stl
Assembly/3D models/Joint 1/Bottom base.stl
Assembly/3D models/Joint 1/Bottom shell.stl
Assembly/3D models/Joint 1/Cable holder 1 (2).stl
Assembly/3D models/Joint 1/Clip 1.stl
Assembly/3D models/Joint 1/Cover 1.stl
Assembly/3D models/Joint 1/Gear 1.5M 20T.stl
Assembly/3D models/Joint 1/M1 mount.stl
Assembly/3D models/Joint 1/Middle shell.stl
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

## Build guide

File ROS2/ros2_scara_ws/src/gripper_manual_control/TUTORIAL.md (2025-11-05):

# Tutorial for controlling the gripper through the robot from a Windows machine

This tutorial is a compilatio of the README files in this repository and specific to just controlling the gripper from a Windows machine.

## Network
After turning on the robot, the Raspberry Pi will search for a WIFI network with the the following credentials:  
**SSID**: DALSA_IOT  
**Password**: dalsa_iot  

Create this using the Windows Mobile Hotspot.
In the hotspot settings you will see when the RPI has connected and its IP adress.

## Logging in Remotly
To execute programs on the RPI you have to log in remotely using SSH. On Windows open the command prompt terminal by searching for "cmd" in the start menu.

In the terminal log in to the RPI by establishing a SSH connection as follows:
```bash
ssh scara@<ip-adress>
```
Type the password **dtubio** when prompted and hit enter.

## Executing the gripper control example program
navigate to the ROS workspace:
```bash
cd bioscara/ROS2/ros2_scara_ws
```
Source the ROS executables:
> [!NOTE]
>
> The following step needs only to be done once after opening a new terminal session or when the 'Package 'gripper_manual_control' not found' error is shown.
```bash
source install/local_setup.sh
```

And finally execute the gripper example program:
```bash
ros2 run gripper_manual_control manual_control
```

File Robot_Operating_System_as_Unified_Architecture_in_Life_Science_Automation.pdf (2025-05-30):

✐

✐ | “output” — 2025/5/2 — 8:39 — page 1 — #1
✐

✐

✐
✐

✐
✐

### DTU Electro Department of Electrical and Photonics Engineering

# Robot Operating System Middleware in System Architecture for Lab Automation

### Sebastian Storz¹ , Xinxin Zhang

1

### , Vilhelm Krarup Møller

2
1 Technical University of Denmark, Department of Electrical and Photonics Engineering, Kgs. Lyngby, Denmark 2 Technical University of Denmark, Department of Biotechnology and Biomedicine, Kgs. Lyngby, Denmark

1 Motivation

Increase laboratory autonomy using task specific machines and general-purpose robots:
– Generalize device agnostic equipment interfaces – Mapping process level and automation level
– Definition and implementation of a multi-layer reference automation framework, like LAPP

A

2 System Architecture

The referenced LAPP framework utilizes both SiLa as a device communication protocol and ROS2 as a robotics middleware. Table 2 shows a blueprint of which features to expose at which abstraction level.

Table 1: The role of ROS2 in the LAPP framework. The example is a general-purpose robot used for liquid transfer.
Protocol | Controller Level [Location] | Methods
SiLa SiLa | Automation Scheduler [Lab] Action Controller [Arm] | Task – Transfer labware Action – pick – place

ROS-SiLa Bridge: SiLa Server & ROS Client ROS2 Motion Sequencer
[Arm]

Motion Sequence
– follow trajectory
sequence
– grip labware
ROS2 (MoveIt) | Motion Controller
[Arm]

Motion Primitives
– follow trajectory
(joint/cartesian)
– get/set gripper
width
Hardware Interface (Custom/Manufacturer Provided)
I2C, UART, CAN, ... | Embedded (Sensors/Actuators) [Joint]
Joint Primitives
– get/set joint
position/velocity
– get/set gripper
joint position

Robot Operating System (ROS2) Collection of open software libraries and tools for robotic control. Role of a middleware, bridging the gap between device specific automation control and device-agnostic procedures. Industry standard in research and highly active development community. Deploying ROS2 to all general-purpose manipulators in the lab reduces necessity of custom drivers. Hardware manufacturers publish control packages for their products to promote interoperability.

Standardization in Lab Automation (SiLa) Open, device agnostic communication standard for laboratory automation on abstract process levels. Devices can expose a SiLa Server which wraps the device API ensuring compatibility with a broader range of clients.

3 BIOSCARA - DIY Robotic Manipulator With a total material cost of 6000 kr. a low-cost labware handling robot used for testing and validation of autonomous workflows. Currently undergoing modification to deploy the ROS2 middleware which includes writing a custom hardware interface. Target scenario could be machine tending with a Opentron liquid handler.

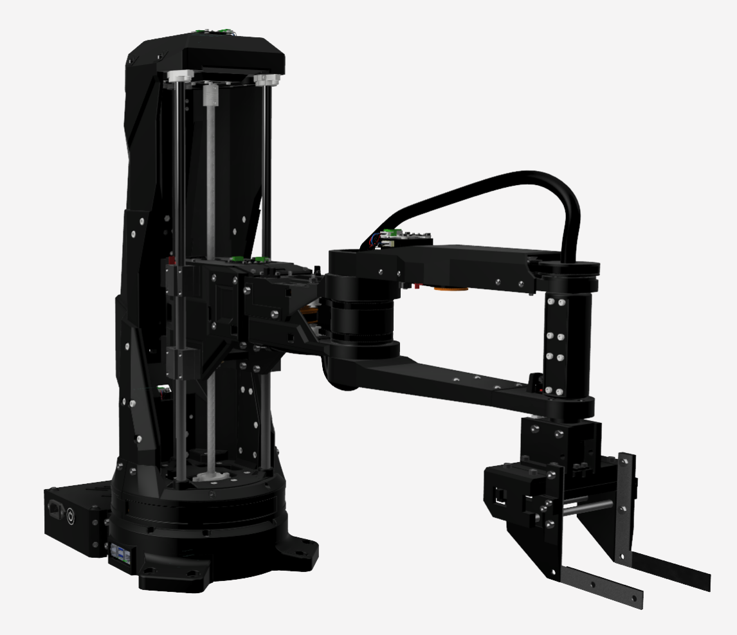
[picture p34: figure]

Figure 1: Bioscara - The DIY SCARA Manipulator
AZsoldos, Wolf, Széll, Galambos, Towards robotic Laboratory Automation Plug & Play: LAPP reference implementation with the TIAGo mobile manipulator, SLAS Tech., Vol. 31, 2025

✐

✐ | “output” — 2025/5/2 — 8:39 — page 2 — #2
✐

✐

✐
✐

✐
✐

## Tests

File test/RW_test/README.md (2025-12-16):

# Communication Read/Write speed test
The realtime performance tests described in the [realtime test](../RT_test/README.md) showed slow execution times for both the read and write cycle. To be precise the test measured the following average cumulative execution times for all joints:
- **Read** (*getPosition*): 3575 μs
- **Write** (*setPosition*): 5062 μs

> [!NOTE]
>
> When conducting the realtime test the position joint trajectory controller was used. In the latest iteration the velocity joint trajectory controller is used. 

This test is to identify the bottleneck that causes the long execution times and to investigate if they can be increase to enable higher controller update rates.

## Description
The test consists of two units:
### Joint Firmware
<!-- TODO: describe and link how to flash firmware  -->
A firmware variant ([profiling_test.ino](../../lib/joint_firmware/profiling_test/profiling_test.ino)) is flashed on the joint controller. This firmware times the execution of the `non_blocking_handler()` which handles the incoming commands and prints the results to the serial port in CSV format. The development machine stays connected to the joint via USB to capture the serial port output and save it to a file. The [Realterm](https://sourceforge.net/projects/realterm/) software was used to cpature and save the serial output. 
### Controller
<!-- TODO: describe and link how to build and source workspace  -->
The controller executes the system_test_packages/comm_speed_test program
```bash
cd ~/bioscara/lib/ros2_ws
ros2 run comm_speed_test main
```

<!-- TODO: write documentation for test program, link or reference here -->
The test program calls times the read and write execution of either position or velocity (`getPosition()`/getVelocity/() and `setPosition()`/setVelocity/() respectively) for a total of 1000x cycles per joint and prints the collected data to a CSV file.

No prints and other unneccessary functions are executed in the timed sections.

## Background
### I2C Protocol
The robot controller and joints communicat via an I2C bus. [This](https://www.ti.com/lit/an/slva704/slva704.pdf) document describes the protocol in detail, below the transmitted bytes are summarized in Table 1 below. Counting the number of transmitted bits is important since the I2C bus clock runs at a speed of 100 kHz (100 kbit/s) or 400 kHz (400 kbit/s).

|Sender| | | | | | | | | | | | | | | | | | | | | | Bits |
| ---- | ---- | --- | ----- | ---- | --- | ---- | --- | ---- | ---- | --- | ---- | ---- | --- | ----- | ---- | --- | ---- | ---- | --- | ----- | ---- | --- |
|*Controller* | S[1] | Addr[7] | Re[1] | | Reg[8] | | TX*1*[8] | | ...  | TX*m*[8] | | S[1] | Addr[7] | Re[1] | | | A[1] | ...  | | NA[1] | P[1] | 27+*n*+8\**m* |
|*Target* | | | | A[1] | | A[1] | | A[1] | ...  | | A[1] | | | | A[1] | RX*1*[8] | | ...  | RX*n*[8] | | | 3+8\**n*+*m* |
| | | | | | | | | | | | | | | | | | | | | | | **30+9\**n*+9\**m*** |

**Table 1:** I2C transmission frames for a combined Read/Write. The number in [n] brackets are the number *n* of transmitted bits in this frame.

> [!NOTE]
>
> The sum of bits in Table 1 is only true for combined Read/Write transmission. In this application every transmission is a Read/Write transmission since at a minimum the return flags are always read from the joint. For a single write transmission with *m* transmitted bytes, the total number of transmitted bits is slightly different (repeated start and repeated address are ommited) and given as follows: *Controller* sends: 18+8\**m* bits, *Target* sends: 2+*m* bits, in **total:** 20+9\**m* bits are transmitted.

### Transmission Speed for set/get Position/Velocity
For the transmissions (get/set Position/Velocity) in questions float values of 4 byte size are transmitted:
| |Write Bytes *m*|Read Bytes *n*| Total Bytes | Total Bits |
| ---- | ----: | ----: | ----: |  ----: |
|`setPosition()`/`setVelocity()`| target [float]  4 | flags [uint8_t]  1 | 5 | 75 |
|`getPosition()`/`getVelocity()`| 0 |  value [float] + flags [uint8_t] 4 + 1 | 5 | 75 |

**Table 2:** Number of bytes and bits transmitted per function.

At the '*Standard Mode*' speed of 100 kbit/s the transmission of 75 bits takes then: **$t_{trans}$ = 750 μs** <br>
At the '*Fast Mode*' speed of 400 kbit/s the transmission of 75 bits takes then: **$t_{trans}$ = 187.5 μs**

## Total Execution time
The total execution time $t_{total}$ which was measured in the realtime-test is the sum of of the following contributions:
- Transmission $t_{trans}$: The formerly calculated theoretical tranmission time via I2C.
- Firmware execution time $t_{exec}$: The duration between receiving the command on the firmware, processing it in the `non_blocking_handler()` returning the state flags.
- Overhead $t_{oh}$: Similar to $t_{exec}$, program overhead, for example memory allocation or similar.
- Noise $t_{noise}$: Delays outside the programs control, for example preemptions.

$$
t_{total} = t_{trans} + t_{exec} + t_{oh} +t_{noise}
$$

## Tests
A series of individual tests have been conducted to gather the relevant data to determine the contributing factors described in the previous section.
- set/getPosition at 100 kHz
    - File: *[position_100khz.csv](position_100kHz.csv)*
- set/getPosition at 400 kHz
    - File: *[position_400khz.csv](position_400kHz.csv)*
- set/getVelocity at 100 kHz
    - File: *[velocity_100khz.csv](velocity_100kHz.csv)*
- set/getVelocity at 400 kHz
    - File: *[velocity_400khz.csv](velocity_400kHz.csv)*
- set/getPosition at 400 kHz, execution time on firmware.
    - File: *[baseline_joint_400khz.csv](baseline_joint_400kHz.csv)*

Addtionally the I2C waveform on the SDA and SCL line has been measured with an oscilloscope to judge if the Raspberry Pi 4 is capable of driving the bus with the given cable length at 400 kHz.
## Results
### Total Time
<table>
  <tr>
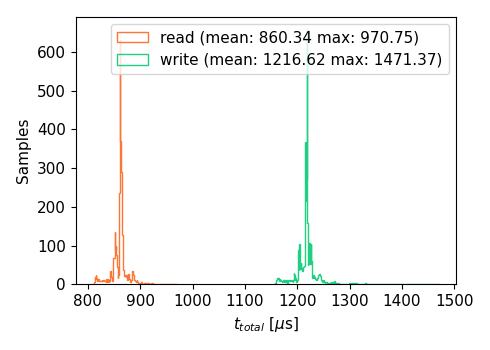
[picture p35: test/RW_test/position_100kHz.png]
    <td><center><strong>Figure 1(a):</strong> Histogram of total time of get/setPosition() at 100 kHz</td>
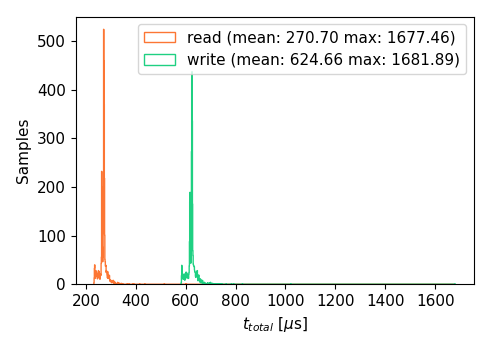
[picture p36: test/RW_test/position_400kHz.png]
    <td><center><strong>Figure 1(b):</strong> Histogram of total time of get/setPosition() at 400 kHz</td>
  </tr>
   <tr>
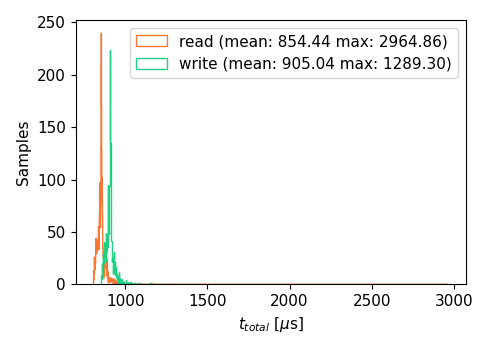
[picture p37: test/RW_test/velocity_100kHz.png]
    <td><center><strong>Figure 1(c):</strong> Histogram of total time of get/setVelocity() at 100 kHz</td>
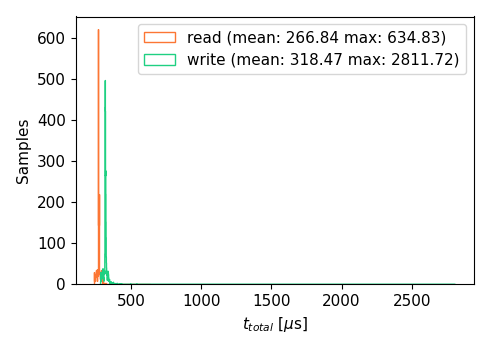
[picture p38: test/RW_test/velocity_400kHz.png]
    <td><center><strong>Figure 1(d):</strong> Histogram of total time of get/setVelocity() at 400 kHz</td>
  </tr>
</table>

<br> 

The results are summarized in Table 3 below:
| Speed Mode [kHz] |Function | Mean [μs] | Max [μs] |
| ---- | ---- | ----: | ----: |
|100|`getPosition()`|860.34 | 970.75|
||`setPosition()`| 1216.62|1471.37|
||`getVelocity()`| 854.44 | 2964.86|
||`setVelocity()`| 905.04|2964.86|
|  |  |  |  |
|400| `getPosition()`| 270.70 | 1677.46|
|| `setPosition()` | 624.66|1681.89|
|| `getVelocity()` | 266.84 | 634.83|
|| `setVelocity()` | 318.47|2811.72|

**Table 3:** Mean and Max total time $t_{total}$ at different transmission speeds and for velocity and position

There is an interesting feature: The `setPosition()` method takes significantly longer than all other functions at a given speed. Furthermore the difference between mean total time for `setPosition()` and `getPosition()` at 100 kHz and 400 kHz is 357 μs and 354 μs respectively, basically identical regardless of the transmission speed. All other functions are somewhat equally fast at their repective transmission speed.

### Execution Time on Firmware
The test was conducted at 400 kHz, however this has no effect since the test only times the execution time between transmission parts.

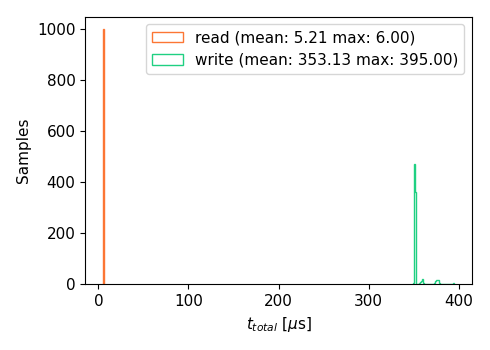
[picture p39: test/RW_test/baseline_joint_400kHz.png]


**Figure 2:** Histogram of the execution time of the position set and get method on the firmware.

This test clearly shows the reason for the much longer $t_{total}$ for `setPosition()`: The corresponding function on the joint firmware itself takes on average $t_{exec}$ = 351.13 μs, while the corresponding function to `getPosition()` only takes  $t_{exec}$ = 5.21 μs on average. exactly the difference previously described. The execution on the joint takes hence 345.92 μs longer on the joint, very close the discrepancy in $t_{total}$.

There is no data for the $t_{exec}$ for `setVelocity()` and  `getVelocity()`, however from the total time it can be deduced that the execution time is similar to $t_{exec}$ for `getPosition()`, since they are relatively close.

this leaves finally the calculation of overhead and noise:<br>
$$
t_{oh} + t_{noise}  = t_{total} - t_{exec} - t_{trans} 
$$

|Speed |Methods|$t_{oh} + t_{noise}$ [μs]|
|---|---|---:|
|100|`getPosition()`|105|
||`setPosition()`|113|
||||
|400|`getPosition()`|84|
||`setPosition()`|78|

**Table 4:** Noise and overhead calculation results.

Table 4 shows that the calculated noise and overhead are only to little degree dependent on transmission speed, and remain somewhat constant. This is expected for the software overhead.

### I2C Waveform
The Inter-Integrated-Circuit (I2C) protocol was as the name suggest never designed to communicate over long distances, however in this applications the wire length accumulates to around 4 m. The long cable length introduces a large capacitance which has to be driven by the Raspberry Pis 1.8 kΩ pul-up resistors. The faster the I2C speed the faster the charge has to be removed and applied, if the capacitance is too large the waveform will become distorted, and in the worst case when the bit value is read, it has not yet reached the HIGH or LOW value.

The oscilloscope screen captures show that the waveform at 400 kHz already looks distorted but crucially the SDA seems to reach the HIGH/LOW state when the SCL signal becomes high. It is at this point the bit is sampled as 0 or 1. From this analysis it is concluded that the I2C bus could be driven at 400 kHz.

<table>
  <tr>
    <td><center><strong>Figure 3(a):</strong> Waveform of SCL (blue) and SDA (yellow) of the I2C bus 100 kHz</td>
  </tr>
   <tr>
    <td><center><strong>Figure 3(b):</strong> Waveform of SCL (blue) and SDA (yellow) of the I2C bus 400 kHz</td>
  </tr>
</table>

There are two limitations: 
- The oscilloscope has a too low sampling frequency to judge the 400 kHz waveform correctly
- The potential result driving the bus at 400 kHz could be a bit flip, which could would go unchecked since to checksum is implemented in the communication protocol to save bytes. A bit flip could have destructive results.

## Discussion
This test has been conducted to investigate if it is possible to increase the controller frequency to achieve better performance and to determine if velocity control is feasible.

### Velocity based Control
This controller relies on a closed loop feedback and calculates joint velocity commands through a PID loop. This has the advantage that it eliminates tracking error for ramp inputs. See the [tracking_error test](../tracking_error/README.md). For this reason the velocity controller is preferential, but it requires a higher controller frequency for a given joint speed to be able timely compute new velocity commands.

The controller needs to:
- Read:
  - Joint velocity
  - Joint position
- Write:
  - Joint velocity

| Method | $t_{total}$ (100 kHz) [μs]| $t_{total}$ (400 kHz) [μs]|
| --- |---: |---: |
|`setVelocity()` | 905  |319  |
|`getVelocity()` | 853  |267  |
|`getPosition()` | 860  | 625  |
| per joint *subtotal* | 2,618  |1,211  |
| 4 joint **total** | 10,472 | 4,844  |

**Table 5:** Expected total times for the velocity based controller.

### Velocity based Control
The simplest joint controller simply forwards position commands to the hardware. The controller is non as such since there is no feedback loop. This drastically lightens the requirements on the robot controllers realtime capability and controllers update frequency. However it leaves all the closed loop control to the joint firmware which has a much less advanced internal control loop. This results in a steady state tracking error for a ramp position reference.

The controller needs to:
- Read:
  - Joint position
- Write:
  - Joint position

| Method | $t_{total}$ (100 kHz) [μs]| $t_{total}$ (400 kHz) [μs]|
| --- |---: |---: |
|`setPosition()` |  1,217  |625  |
|`getPosition()` | 860  | 271  |
| per joint *subtotal* |2,077|896|
| 4 joint **total** |8,308|3,584|

**Table 6:** Expected total times for the position based controller.

### Scheduler Priority
The comm_speed_test program is run without realtime priorities and hence can be subject to preemption of higher priority threads. This will have an impact on worst case execution times but over 1000 samples the impact will be reduced. For this reason the max values have not been taken into consideration. It is assumed that they will be drastically reduced when running with a realtime priority, which the ros2_control node is.

### Final Discussion on I2C Bus speed
Although it is possible to run at 400 kHz I2C bus speed, long term reliability tests are still outstanding to proove that no communication errors occur. For now the I2C speed remains at the much more robust 100 kHz.

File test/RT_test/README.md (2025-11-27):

# Analyzing realtime requirements
This test is to analyze the impact of Kernel configurations on the execution times of the ros2_control main update loop. Missed deadlines could lead to poor controller performance.

## Original Approach (idea)
Cyclictest, why? common tool

Run in parallel to application. (recommended)

priority higher than ROS2_control? to measure the effect it would experience. otherwise that process would influence the latency of the measurement.

With and without Rviz

with and without realtime group

Ros control tries to use FIFO scheduling (RT scheduling class) at prio (higher is higher prio)

https://man7.org/linux/man-pages/man7/sched.7.html

https://blogs.oracle.com/linux/post/task-priority

cyclictest needs to run as sudo (so it can set any prio...)

without any adjustments ros2_control runs with priority in user space (non-realtime) 20 (0 niceness) or 120 in kernel space.



### Tests

For all tests:

- run ros2_control in parallel with Rviz for worst case test and simulated system load. the test itself adds only minimal overhead.
- --mlockall/-m (Prevent Cyclictest pages from being paged out of memory)
- (run 30 min, the longer the higher the chance to catch max latency)
- (intervall 10ms like 100Hz controller) seems very high
- -S one measuring thread per cpu 

```bash
cyclictest -l100000000 -m -S -p<49/119> -i200 -h400 -q > output
```

1. Non-realtime priority, but higher than ros2_control (just a bit)
2. Add scara user to realtime group so that ros2_conrol can run as RT. Repeat with RT priority 51 for example, just slightly higher than Rviz runs at

Assumption:

in case (1) latency in the range of + 3ms

in case (2) no missed deadlines

## Problem

cyclictest only works with RT policies, so I cant test with non rt prio 19 for example

## Alternative Approach:
Directly collect statistics from the controller managers statistics diagnostics output. */controller_manager/statistics/*

### Update Rate

50 Hz -> 20 ms deadline

Assumption, increasing scheduler priority shows effect by reducing read/write times of the hardware interface

### System Load:

following ssh sessions (no X forwarding):

- ros2_control
- trajectory publisher
- ros2 bag recorder

Simple trajectory every 5s:

	every 5 send trajectory:

	j1: 0.0, j2: 0.2, j3: 0.0, j4: 0.0

	j1: 0.7, j2: 0.2, j3: -0.7, j4: 0.7

### Recording:

```bash
ros2 bag record -e ^\/controller_manager.* -o record_<update_rate>_<prio>_<note>
```

10 min recording. The longer the recording the higher the chance to catch an uncommon latency.

After recording export to CSV:
replay topics with:
```bash
ros2 bag play record_<update_rate>_<prio>_<note> -p
``` 
listen and export topics:
```bash
ros2 topic echo /controller_manager/statistics/full --csv > record_<update_rate>_<prio>_<note>.csv
```
#### Test 1
- Position control, prio 20

#### Test 2
Add the user to the realtime group as described [here](../../Raspberry/README.md#adding-the-scara-user-to-realtime-group)

Then execute the test:
- Position control, RT prio 50, FIFO Scheduler (default ROS2 control values)

## Observation
Priority has no effect on execution time. 
Time spans much longer than what is caused through normal system latency.
Instead execution time linearly scales with the number of joints. 

I2C standard mode:
100kbit/s -> 12.5 kByte/s -> 80 us/byte

transmission of set position:
register + sizeof(float) + flags = 6 bytes

all joints:
R: avg 3575 us
W: avg 5062 us

2 joints:
R: avg 1875 us
W: avg 2615 us

3 joints:
R: avg 2697 us
W: avg 3815 us

## Evaluation
- [ ] Make Histogram of execution times
- [ ] Min/Max statistics
- [ ] Compare Max execution time between priorities

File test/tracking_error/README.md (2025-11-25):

# Quantifying the tracking error
This test is to quantify the tracking errors of position inputs with focus on ramp (constant velocity) reference.
The test compares the performance between the JTC with position as command interface and the JTC with velocity as command interface.

## Assumption
Since the postion JTC simply forwards the postion reference to the joint it can be proven using control theory that any ramp reference will have a bounded non-zero steady state error. However when using the velocity JTC the ramp tracking error will be zero since the position error is mapped through a PID controller with feed-forward to the system which takes the velocity as command input. This way the system has one additional integrator which eliminates the ramp following error.

## Tests
Joint 1 is used for all tests. All generated ramps are below the maximum joint speed, which is constant and configured to be 1.0 rad/s.
Two ramps are configured with different speeds:

**Ramp 1**: From -1.5707 rad to 1.5707 rad in 20 s. Yielding a ramp gradient/speed ($\dot{r}_{1}$) of 0.15707 rad/s <br>
**Ramp 2**: From -1.5707 rad to 1.5707 rad in 10 s. Yielding a ramp gradient/speed of 0.31415 rad/s

The following data is collected:
*Position Setpoint* ($r_{1}$) and *Joint Position* ($q_{1}$).

The error is defined as:
$$
e_{1} = \frac{r_1-q_1}{\dot{r}_{1}}
$$

To investigate the effect of the maximum acceleration setting the test is repeated for the acceleration values given below. Note that these are the maximum hardware values to protect the joint from stalling. The final motion planning will use lower acceleration values to create trajectories.
**MaxAccel 1**: 0.157 rad/s^2 <br>
**MaxAccel 2**: 1.57 rad/s^2 <br>

### Controller Parameters
The JTC runs with an update rate of 50 Hz.
For the position test no parameters can be tuned, since the controller directly forwards the trajectory. Neither on the firmware side, since there the setPoint intern is forwarded to the stepper driver which. The stepper does **not** operate in field oriented control FOC.

### Expected Result
Tracking error stays constant relative to ramp but depends linearly on maxAccel

## Recording:

```bash
ros2 bag record -e ^\/controller_manager.* -o record_<ramp_gradient>_<maxAccel>_<note>
```
for example: here also */velocity_joint_trajectory_controller/controller_state* is recorded
```bash
ros2 bag record /controller_manager/introspection_data/full /velocity_joint_trajectory_controller/controller_state -o record_0p15707_1p57_j1_vel_p0p0_i0p0_d
0p0_kff1p0
```
recording one long ramp input is sufficient. 

After recording export to CSV:
replay topics with:
```bash
ros2 bag play record_<ramp_gradient>_<maxAccel>_<note> -p
``` 
listen and export topics:
```bash
ros2 topic echo /controller_manager/introspection_data/full --csv > record_<ramp_gradient>_<maxAccel>_<note>.csv
```

## Results
### Test 1, Position JTC
| | 0.15707 | 0.31415 |
| ---- | --- | ---- |
| 0.157 | ~0.52 |  ~1.0 |
| 1.57  |  ~0.07 |  ~0.12 |

weird, not what expected, error scales with ramp gradient despite normalizing it

### Test 2, Velocity JTC
Steady-state tracking error is zero, where $k_p > 0$

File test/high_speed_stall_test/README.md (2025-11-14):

# High speed stall detection

This test is to examine the performance of the speed adaptive stall threshold.

The speeds are in motor units, not joint units!

## Setup

For an unconstrained joint motor, a ramp from 0 to 120 rad/s

Development: Spikey PID error makes problems. First remove large spikes, then fast LP filter to remove remaining spikes of smaller amplitude. Needs to be fast in particular in low speed regime difficult to detect stall. 

Two regimes with a breakpoint before the "resonance". Reason for systematic increase in PID error in speeds between 15 rad/s and 40 rad/s is unclear. Peak at higher speeds only appears when decelerating.

Tuning the breakpoint might be necessary but it is difficult since all other joints cant move freely. 

Threshold is set relatively high, making threshold linear to speed as well has little impact at high threshold values.

High speed threshold leaves plenty of room. Also when stalling in highspeed regime threshold is pulled down.

SG_RESULT did not indicate stall, further tuning would be necessary but it would also suffer from limited range.

### J3

First up ramp up to 5 rad/s

than down ramp from 5 rad/s. Higher PID error at upper end but could be caused by previous acceleration

using max accel and vel from test

### J2

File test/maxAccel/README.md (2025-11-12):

Generally max acceleration is more subtle than max vel. in the latter the joint stops moving,
Max both can be increased with higher current.

## J1
- hearable skipping when a max at 3/rad/s2
- first signs of degradation at 3rad/s2 and 1 rad/s.
- at 3rad/s2 and 2rad/s joint doesnt reach max velocity

    -> **vmax** = 1 rad/s; **amax** = 2 rad/s2

## J2
- Higher current to allow faster movement. 50%
- Max velocity at 50% current: 0.03 m/s
- At acceleration > 0.2 rad/s2 acceleration drops to 0.08 rad/s2

    -> **vmax** = 0.03 m/s; **amax** = 0.2 m/s2

## J3
- Max velocity determined to be 5 rad/s at 20% current. (run j3_15)
- max accleration at 14 rad/s2 (run j3_17)
- acc 15 rad/s2 and vel 5rad/s didnt work (run j3_18)

    -> **vmax** = 5 rad/s; **amax** = 14 rad/s2

### J4
- Max acceleration between 30 and 34 rad/s (run j4_3 and j4_4)
- Max veloctiy between 10 and 20 rad/s (run j4_5)
- cant test higher velocities as range is insufficient at given acceleration

    -> **vmax** = 10 rad/s; **amax** = 30 rad/s2

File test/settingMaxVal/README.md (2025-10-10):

# Testing the setMaxAccel and setMaxVel functions
The aim of this test is to verify that the setting of maximum acceleration and velocity values is correct, including their conversion through the transmission.

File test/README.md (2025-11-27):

# Test Descriptions and Data
This directory includes test descriptions and test data for conducted system tests.

## Plotting
Go to the tests relevant subdirectory and activate the 
```bash
cd ~/bioscara/test/<test_dir>
source ../.venv/bin/activate
```

If not done already install the requirements from the *requirements.txt* file.
```bash
pip install -r ../requirements.txt
```

### Latex
To be able to use pure latex in matplot install:
```bash
sudo apt-get install texlive-latex-recommended texlive-latex-extra texlive-fonts-recommended dvipng cm-super
```

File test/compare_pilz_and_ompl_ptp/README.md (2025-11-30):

# Comparing Trajectory generation for Point-To-Point Motion between Pilz and OMPL Motion Planner
A test to compare PTP trajectories absent of external constraints between the Pilz Industrial Motion Planner and the OMPL planner.
## Background
The Pilz Industrial Motion Planner (PILZ planner) introduces the new Action/Service *MoveGroupSequenceAction*/*MoveGroupSequenceService*, which allows to concatenate multiple trajectories with an optional blend radius. See the [documentation](https://github.com/moveit/moveit2_tutorials/blob/b0ba2a971d18a024d136ec7b175c7353eb0e02d8/doc/how_to_guides/pilz_industrial_motion_planner/pilz_industrial_motion_pla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) for more details.

The motion sequence is created by individual trajectories for each passed waypoint and subsequently blending them together. Being part of the PILZ planning pipeline the motion sequence has been designed for the use with the one of the PILZ motion planners (planner_id: "LIN","CIRC", and "PTP") in mind. Besides the *planner_id*, the planning request of type *MotionPlanRequest* however also allows, to set the *pipeline_id*. By setting the *pipeline_id* to 'ompl' (the exact name depends on the name the planning pipeline has been given when passed to the move_group on launch) the OMPL motion planner can be invoked to create a sequence segment.

## Problem
The problem arises when the trajectories are being blended. To blend two trajectories ([See how](https://github.com/moveit/moveit2/blob/760277f74ba78bc48f157f7f6c38ac13de4a2721/moveit_planners/pilz_industrial_motion_planner/doc/MotionBlendAlgorithmDescription.pd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)) the first trajectory's last point and second trajectory's first point must have equal position, and zero velocity and acceleration. The PILZ planners create such trajectories, OMPL however do not and hence [this](https://github.com/moveit/moveit2/blob/760277f74ba78bc48f157f7f6c38ac13de4a2721/moveit_planners/pilz_industrial_motion_planner/src/trajectory_blender_transition_wind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) fails. Inhibiting the sequence blender to complete successfully. The trajectory created by OMPL however is a trapezoidal trajectory (absent of other constraints like collisions) and hence SHOULD have zero acceleration at the start and end.

<!-- TODO: write pros and cons of PILZ vs OMPL -->
## Test
To investigate why the blending fails a simple test is conducted. The robot hardware is launch (mock_hardware is sufficient), the move_group and Rviz with the MotionPlanning panel is started. Using the MotionPlanning a new goal position (relatively close to the starting position to avoid long trajectories) is created and a planning request is sent. First to the OMPL and secondly the the PILZ PTP planner. The planners respond with a created trajectory which is logged and plotted using the [plotting script](../traj_plots/README.md).

## Results
The resulting trajectories as created by the planners are plotted below. 
<table>
  <tr>
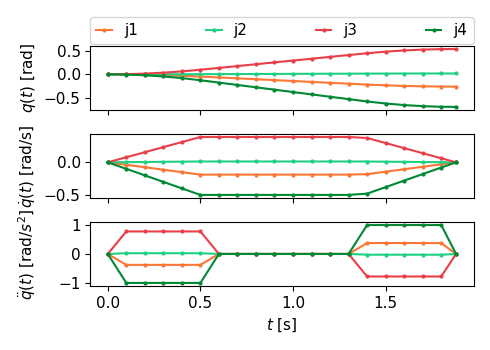
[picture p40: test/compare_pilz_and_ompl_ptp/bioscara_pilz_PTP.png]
    <td><center><strong>Figure 1(a):</strong> Trajectory created by the PILZ PTP planner</td>
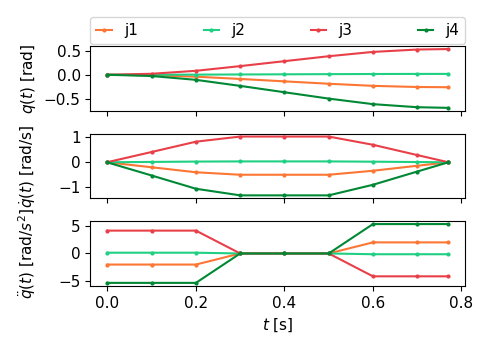
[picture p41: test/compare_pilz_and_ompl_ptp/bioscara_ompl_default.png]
    <td><center><strong>Figure 1(b):</strong> Trajectory created by the OMPL default planner</td>
  </tr>
</table>

There are two striking differences:
1) For the same acceleration and velocity limits the OMPL planner produces a trajectory that takes 0.77 s, while the PILZ PTP trajectory takes 1.88 s.
2) The PILZ trajectory has $\ddot{q} = 0.0$ acceleration at $t = t_0 = 0.0$ s and $t=t_f= 1.88$ s, while the OMPL trajectory has $\ddot{q} \ne 0.0$ acceleration at $t = t_0 = 0.0$ s and $t=t_f= 0.77$ s.

## Discussion
The observation described in (2) is the direct cause for the failing trajectory blend.

The significant execution duration can be attributed to the fact that the PILZ motion planner is choosing a very conservative/non-optimal approach to calculate the trapezoidal trajectory using the strictest [joint limits](https://github.com/moveit/moveit2_tutorials/blob/b0ba2a971d18a024d136ec7b175c7353eb0e02d8/doc/how_to_guides/pilz_industrial_motion_planner/pilz_industrial_motion_pla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). This approach guarantees that no kinematic limits are violated, however does so suboptimally, since the existence of a faster trajectory (the OMPL one) satisfying the same joint limits disproves optimality. This suboptimality, combined with the lacking collision avoidance when using the PILZ PTP planner is a key reason the attempt to create a motion sequence with an alternative planner has been undertaken. Ideally it is possible to leverage the convenient blended sequence with the more advanced OMPL planner.

<!-- TODO: write detailed description of PTP joint limit problem -->
<!-- TODO: Write thoughts on sequence generation. User defined tought waypoints vs collision constrained "pure" OMPL sequence with MTC f.x -->

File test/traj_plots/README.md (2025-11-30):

# Plot moveit_msgs/msg/DisplayTrajectory
This directory contains a python script that can be used to plot a trajectory recorded with ros2 topic echo

## Recording the Trajectory
1) Prepare the Topic recording:
```bash
cd <this_directory>
ros2 topic echo --once /display_planned_path moveit_msgs/msg/DisplayTrajectory > <file_name>.yaml
```
2) Send a planning request of any kind to the MoveIt MoveGroup
3) Call the plotting script, passing the collected data. Activating the venv is only necessary once in the same terminal session.
```bash
source ../.venv/bin/activate
python3 plot_traj.py <file_name>.yaml
```

>[!NOTE]
>
> If the trajectory is too long, `ros2 topic echo` truncates parts of the printed message which will truncate the displayed trajectory as well.

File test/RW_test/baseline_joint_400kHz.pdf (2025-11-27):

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

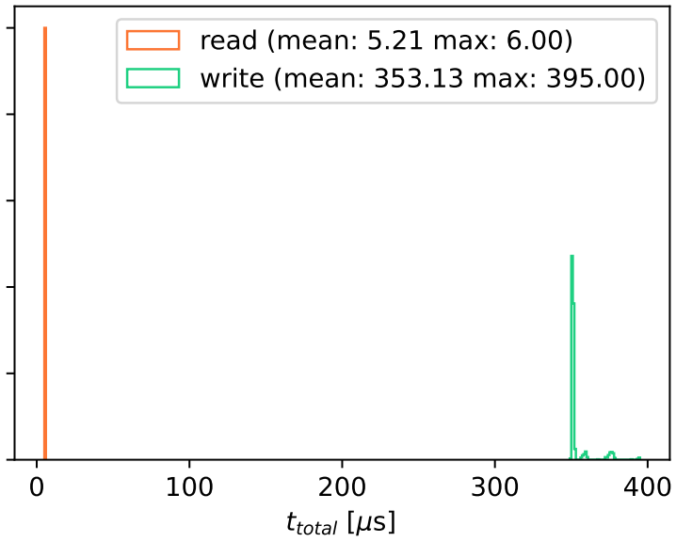
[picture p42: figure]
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

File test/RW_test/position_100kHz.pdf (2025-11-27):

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

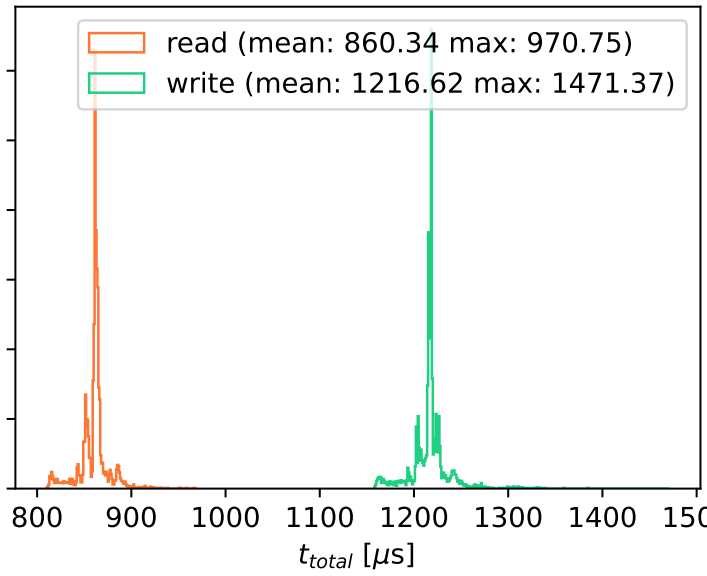
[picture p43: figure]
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

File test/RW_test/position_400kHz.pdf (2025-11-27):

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

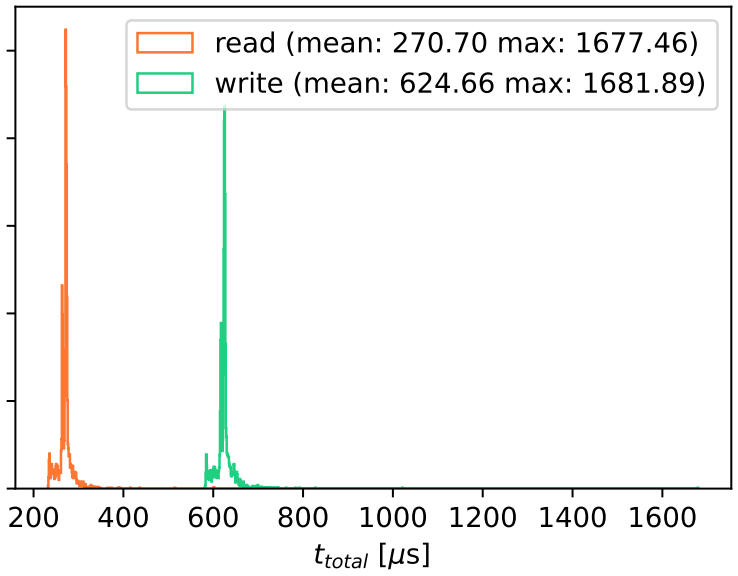
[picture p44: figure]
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

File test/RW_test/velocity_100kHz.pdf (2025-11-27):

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

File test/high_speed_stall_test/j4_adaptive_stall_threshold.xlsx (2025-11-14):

Program Time [s] | raw abs(pid-error) | abs(pid-error) spikes removed | abs(pid-error) spikes removed LP filtered | raw SG_RESULT | SG_RESULT spikes removed | q [deg] | q_set [deg] | qd [rad/s] | qd_set [rad/s] | threshold | stall
52.2413 | 7 | 7 | 12.8 | 74 | 74 | 0 | 0 | 51.34 | 50.76 | 81.39 | 0
52.2627 | 28 | 28 | 14.32 | 86 | 86 | 0 | 0 | 51.27 | 50.64 | 81.36 | 1
52.2632 | 2 | 2 | 13.09 | 81 | 81 | 0 | 0 | 51.22 | 50.52 | 81.34 | 0
52.2721 | 9 | 9 | 12.68 | 81 | 81 | 0 | 0 | 51.06 | 50.4 | 81.28 | 0
52.2823 | 5 | 5 | 11.91 | 86 | 86 | 0 | 0 | 50.89 | 50.28 | 81.21 | 1
52.3009 | 37 | 37 | 14.42 | 89 | 89 | 0 | 0 | 50.84 | 50.16 | 81.18 | 1
52.3024 | 7 | 7 | 13.68 | 83 | 83 | 0 | 0 | 50.8 | 50.04 | 81.17 | 1
52.312 | 20 | 20 | 14.31 | 83 | 83 | 0 | 0 | 50.73 | 50.04 | 81.14 | 1
52.323 | 14 | 14 | 14.28 | 76 | 76 | 0 | 0 | 50.62 | 49.92 | 81.09 | 0
52.3321 | 3 | 3 | 13.15 | 81 | 81 | 0 | 0 | 50.45 | 49.8 | 81.02 | 0
52.3421 | 12 | 12 | 13.04 | 86 | 86 | 0 | 0 | 50.31 | 49.68 | 80.96 | 1
52.3524 | 24 | 24 | 14.13 | 89 | 89 | 0 | 0 | 50.21 | 49.56 | 80.92 | 1
52.3621 | 4 | 4 | 13.12 | 80 | 80 | 0 | 0 | 50.15 | 49.44 | 80.89 | 0
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

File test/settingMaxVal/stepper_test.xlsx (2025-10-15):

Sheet: Sheet2 (2)
maxAccel: 10000000.000000
maxVel: 200000.000000
time | position | velocity | accleration
0.00 | 0.00 | 0.002882 | 0.00 | 9678.68
0.01 | 0.54 | 3.07 | 223.54
0.03 | 2.60 | 22.34 | 1614.02
0.04 | 5.72 | 61.36 | 3262.07
0.05 | 10.17 | 107.77 | 3877.34
0.06 | 15.82 | 170.42 | 5252.80
0.07 | 23.14 | 238.73 | 5722.59
0.09 | 31.54 | 314.52 | 6311.55
0.10 | 41.73 | 401.97 | 7350.83
0.11 | 51.69 | 485.03 | 6979.19
0.12 | 63.96 | 579.87 | 7890.26
0.13 | 78.74 | 673.49 | 7751.64
0.15 | 92.56 | 771.30 | 8239.18
0.16 | 108.59 | 869.44 | 8235.87
0.17 | 124.93 | 969.28 | 8353.34
0.18 | 144.78 | 1079.10 | 9142.48
0.19 | 164.52 | 1182.28 | 8647.58
0.20 | 185.57 | 1290.89 | 9120.97
0.22 | 209.09 | 1396.25 | 8845.83
0.23 | 232.49 | 1505.61 | 9113.54
0.24 | 258.01 | 1606.27 | 8391.74
0.25 | 283.78 | 1712.06 | 8821.91
0.26 | 312.55 | 1817.43 | 8865.95
0.28 | 341.19 | 1926.54 | 9100.01
0.29 | 370.83 | 2038.68 | 9387.34
0.30 | 403.30 | 2142.39 | 8670.76
0.31 | 435.04 | 2248.84 | 8913.27
0.32 | 470.17 | 2350.80 | 8539.43
0.34 | 505.10 | 2457.91 | 8975.38
0.35 | 541.03 | 2571.09 | 9488.17
0.36 | 580.39 | 2679.02 | 8975.17
0.37 | 618.44 | 2788.04 | 9119.69
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

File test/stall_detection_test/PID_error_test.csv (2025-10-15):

Program Time [s] | PID error | Threshold | q | q_set | Stalled
6033.77 | 1 | 200 | -0.01 | 0 | 0
6033.78 | 2 | 200 | 0 | 0 | 0
6033.79 | 2 | 200 | 0 | 0 | 0
6033.8 | 3 | 200 | 0 | 0 | 0
6033.81 | 3 | 200 | 0 | 0 | 0
6033.82 | 3 | 200 | 0 | 0 | 0
6033.83 | 4 | 200 | 0 | 0 | 0
6033.84 | 1 | 200 | -0.01 | 0 | 0
6033.85 | 2 | 200 | 0 | 0 | 0
6033.86 | 1 | 200 | -0.02 | 0 | 0
6033.87 | 2 | 200 | -0.02 | 0 | 0
6033.88 | 2 | 200 | 0 | 0 | 0
6033.89 | 2 | 200 | 0 | 0 | 0
6033.9 | 2 | 200 | 0 | 0 | 0
6033.91 | 2 | 200 | -0.01 | 0 | 0
6033.92 | 1 | 200 | -0.01 | 0 | 0
6033.93 | 3 | 200 | 0.01 | 0 | 0
6033.94 | 3 | 200 | -0.01 | 0 | 0
6033.95 | 4 | 200 | 0 | 0 | 0
6033.96 | 3 | 200 | 0.01 | 0 | 0
6033.97 | 2 | 200 | 0.01 | 0 | 0
6033.98 | 1 | 200 | -0.01 | 0 | 0
6033.99 | 0 | 200 | 0 | 0 | 0
6034 | 0 | 200 | 0 | 0 | 0
6034.01 | 0 | 200 | -0.01 | 0 | 0
6034.02 | 0 | 200 | 0 | 0 | 0
6034.03 | 1 | 200 | 0 | 0 | 0
6034.04 | 1 | 200 | 0 | 0 | 0
6034.05 | 1 | 200 | 0 | 0 | 0
6034.06 | 0 | 200 | -0.01 | 0 | 0
6034.07 | 1 | 200 | 0 | 0 | 0
6034.08 | 1 | 200 | 0 | 0 | 0
6034.09 | 0 | 200 | 0 | 0 | 0
6034.1 | 1 | 200 | 0 | 0 | 0
6034.11 | 2 | 200 | 0.01 | 0 | 0
6034.12 | 1 | 200 | -0.01 | 0 | 0
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

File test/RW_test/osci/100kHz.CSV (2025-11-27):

SDA | SCL | 1.0uS
175 | 178
174 | 178
182 | 182
180 | 185
184 | 184
181 | 185
184 | 185
181 | 185
184 | 185
181 | 185
185 | 184
182 | 186
184 | 185
180 | 186
184 | 184
180 | 185
182 | 184
179 | 185
182 | 184
180 | 185
182 | 184
179 | 184
184 | 184
179 | 184
184 | 184
181 | 185
184 | 184
181 | 185
184 | 182
181 | 185
184 | 183
180 | 184
182 | 184
179 | 184
181 | 182
179 | 185
182 | 182
179 | 184
182 | 182
181 | 185
184 | 184
181 | 185
185 | 184
183 | 185
185 | 184
182 | 184
184 | 183
180 | 185
182 | 183
179 | 184
182 | 183
178 | 184
182 | 182
179 | 184
182 | 182
180 | 184
184 | 184
181 | 185
185 | 184
182 | 185
185 | 184
182 | 185
184 | 184
181 | 185
183 | 182
180 | 184
182 | 182
179 | 184
182 | 182
179 | 184
182 | 182
179 | 184
182 | 184
180 | 185
184 | 184
181 | 185
185 | 184
181 | 185
184 | 184
181 | 185
184 | 182
181 | 185
182 | 182
180 | 184
182 | 182
179 | 184
184 | 184
179 | 185
183 | 184
181 | 187
184 | 184
181 | 185
184 | 184
181 | 185
184 | 184
181 | 185
184 | 182
181 | 184
183 | 182
179 | 184
184 | 182
179 | 184
182 | 182
179 | 184
182 | 182
179 | 184
184 | 185
181 | 187
182 | 182
181 | 184
185 | 184
181 | 185
182 | 182
181 | 184
182 | 184
180 | 184
182 | 182
179 | 184
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

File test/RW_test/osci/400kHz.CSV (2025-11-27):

SDA | SCL | 1.0uS
172 | 175
173 | 176
181 | 182
178 | 184
182 | 182
179 | 184
183 | 182
181 | 184
184 | 184
181 | 185
184 | 184
181 | 184
184 | 184
180 | 184
182 | 183
179 | 184
182 | 184
179 | 184
182 | 182
179 | 184
182 | 182
179 | 184
182 | 182
181 | 184
184 | 182
181 | 184
184 | 182
180 | 184
184 | 184
180 | 184
182 | 182
179 | 184
182 | 182
179 | 184
182 | 182
179 | 184
182 | 182
179 | 184
184 | 184
181 | 184
184 | 183
181 | 184
184 | 184
180 | 184
182 | 182
181 | 184
184 | 182
179 | 185
182 | 182
179 | 184
182 | 182
181 | 184
182 | 182
180 | 184
183 | 182
180 | 184
182 | 182
181 | 185
182 | 182
180 | 184
182 | 182
179 | 184
182 | 184
181 | 184
184 | 182
180 | 184
182 | 182
180 | 184
182 | 182
180 | 185
184 | 184
181 | 184
182 | 183
180 | 184
184 | 183
180 | 184
182 | 183
180 | 184
182 | 182
179 | 184
182 | 183
179 | 184
182 | 182
180 | 185
184 | 182
181 | 185
185 | 184
182 | 185
185 | 184
182 | 185
185 | 185
181 | 185
182 | 182
179 | 184
182 | 182
179 | 184
182 | 182
179 | 185
182 | 182
179 | 184
182 | 182
179 | 184
184 | 183
181 | 185
185 | 185
182 | 186
184 | 184
179 | 182
183 | 182
181 | 184
182 | 184
180 | 185
182 | 183
179 | 184
182 | 182
179 | 184
182 | 184
179 | 184
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

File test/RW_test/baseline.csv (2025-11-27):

time [ms] | iteration [-] | joint [-] | read [us] | write[us]
2.108939 | 1 | j4 | 869.528000 | 1235.264000
4.212879 | 1 | j3 | 859.305000 | 1214.894000
6.334559 | 1 | j2 | 860.472000 | 1236.912000
8.396184 | 1 | j1 | 853.694000 | 1194.394000
10.460143 | 2 | j4 | 844.731000 | 1194.413000
12.545953 | 2 | j3 | 864.880000 | 1208.802000
14.664892 | 2 | j2 | 861.065000 | 1232.523000
16.750202 | 2 | j1 | 852.342000 | 1210.986000
18.822512 | 3 | j4 | 845.490000 | 1214.079000
20.893267 | 3 | j3 | 852.139000 | 1205.060000
22.965577 | 3 | j2 | 854.009000 | 1205.097000
25.032758 | 3 | j1 | 849.917000 | 1204.320000
27.111865 | 4 | j4 | 853.416000 | 1212.542000
29.199749 | 4 | j3 | 852.176000 | 1222.857000
31.295874 | 4 | j2 | 866.176000 | 1215.468000
33.422702 | 4 | j1 | 893.712000 | 1218.727000
35.544345 | 5 | j4 | 861.583000 | 1244.727000
37.647136 | 5 | j3 | 864.508000 | 1223.171000
39.741928 | 5 | j2 | 865.417000 | 1214.912000
41.835831 | 5 | j1 | 864.101000 | 1215.524000
43.929770 | 6 | j4 | 863.712000 | 1215.023000
46.023525 | 6 | j3 | 863.213000 | 1215.802000
48.124075 | 6 | j2 | 863.361000 | 1222.579000
50.219645 | 6 | j1 | 865.861000 | 1215.190000
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

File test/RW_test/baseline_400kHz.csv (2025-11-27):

time [ms] | iteration [-] | joint [-] | read [us] | write[us]
0.988352 | 1 | j4 | 295.961000 | 687.982000
1.964108 | 1 | j3 | 293.571000 | 648.361000
2.972706 | 1 | j2 | 287.311000 | 699.096000
3.898746 | 1 | j1 | 277.049000 | 627.912000
4.807653 | 2 | j4 | 270.362000 | 623.708000
5.721208 | 2 | j3 | 275.863000 | 624.985000
6.635468 | 2 | j2 | 273.603000 | 626.078000
7.560694 | 2 | j1 | 269.010000 | 643.972000
8.466266 | 3 | j4 | 269.973000 | 622.411000
9.302488 | 3 | j3 | 240.559000 | 584.476000
10.133876 | 3 | j2 | 242.744000 | 582.994000
10.956650 | 3 | j1 | 233.816000 | 583.105000
11.780481 | 4 | j4 | 233.742000 | 584.272000
12.602162 | 4 | j3 | 232.538000 | 583.216000
13.424789 | 4 | j2 | 233.409000 | 583.754000
14.247267 | 4 | j1 | 234.964000 | 581.827000
15.071115 | 5 | j4 | 233.650000 | 584.420000
15.895761 | 5 | j3 | 232.631000 | 586.310000
16.719480 | 5 | j2 | 234.149000 | 583.790000
17.587932 | 5 | j1 | 232.871000 | 629.912000
18.495042 | 6 | j4 | 269.455000 | 624.319000
19.401078 | 6 | j3 | 270.733000 | 622.726000
20.308280 | 6 | j2 | 273.363000 | 620.892000
21.215001 | 6 | j1 | 272.752000 | 621.503000
22.122722 | 7 | j4 | 268.751000 | 626.467000
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

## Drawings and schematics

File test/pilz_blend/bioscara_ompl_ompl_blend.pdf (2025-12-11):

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

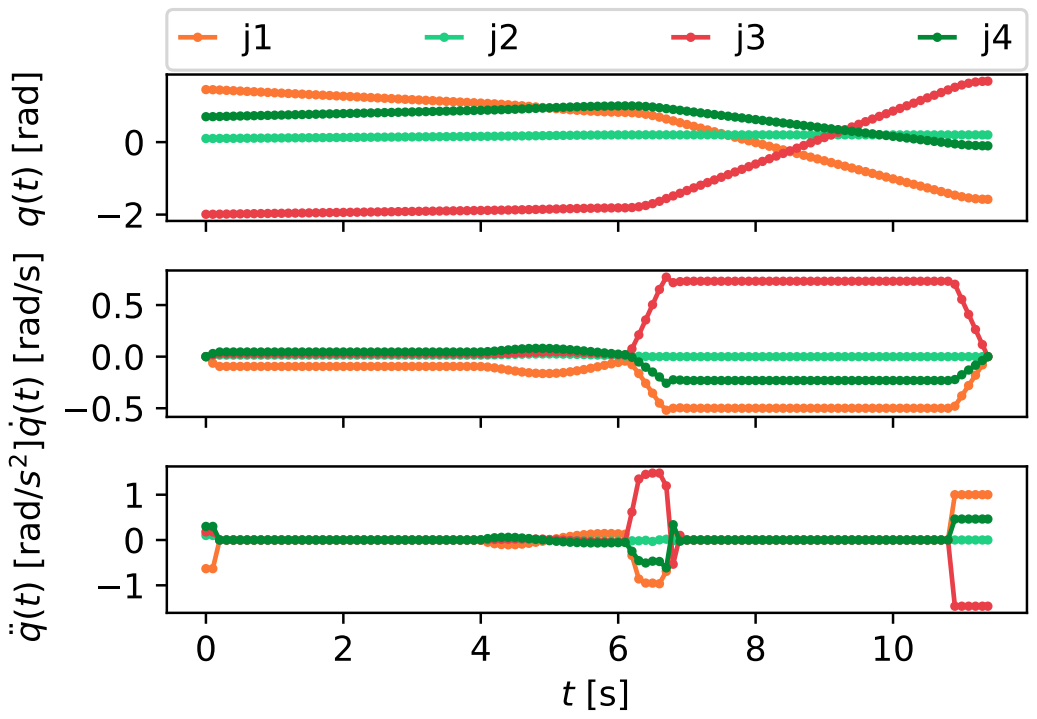
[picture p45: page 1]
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

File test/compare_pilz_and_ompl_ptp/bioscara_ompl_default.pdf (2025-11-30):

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

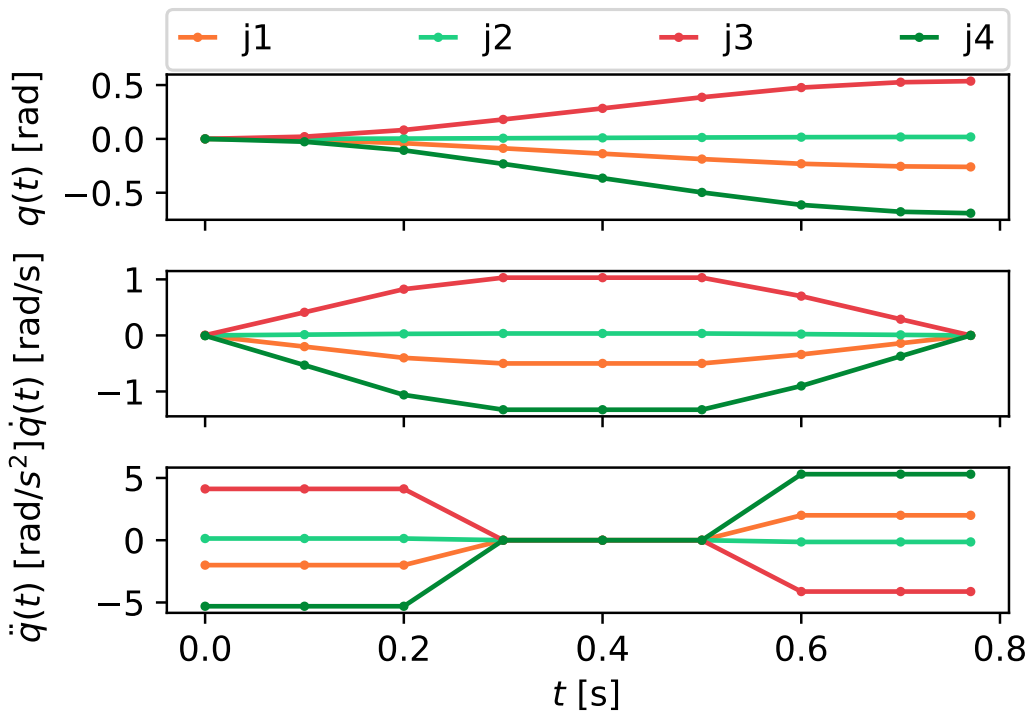
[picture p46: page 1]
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

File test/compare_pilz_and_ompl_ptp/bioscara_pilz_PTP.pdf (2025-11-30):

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

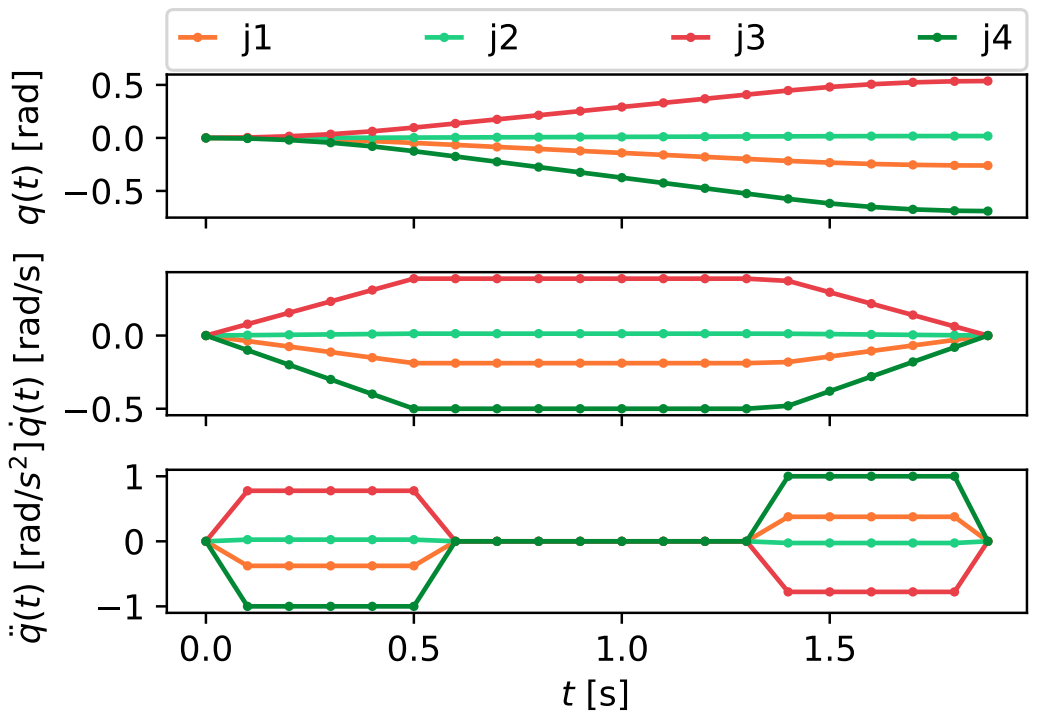
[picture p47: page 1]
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

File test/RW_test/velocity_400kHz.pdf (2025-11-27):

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

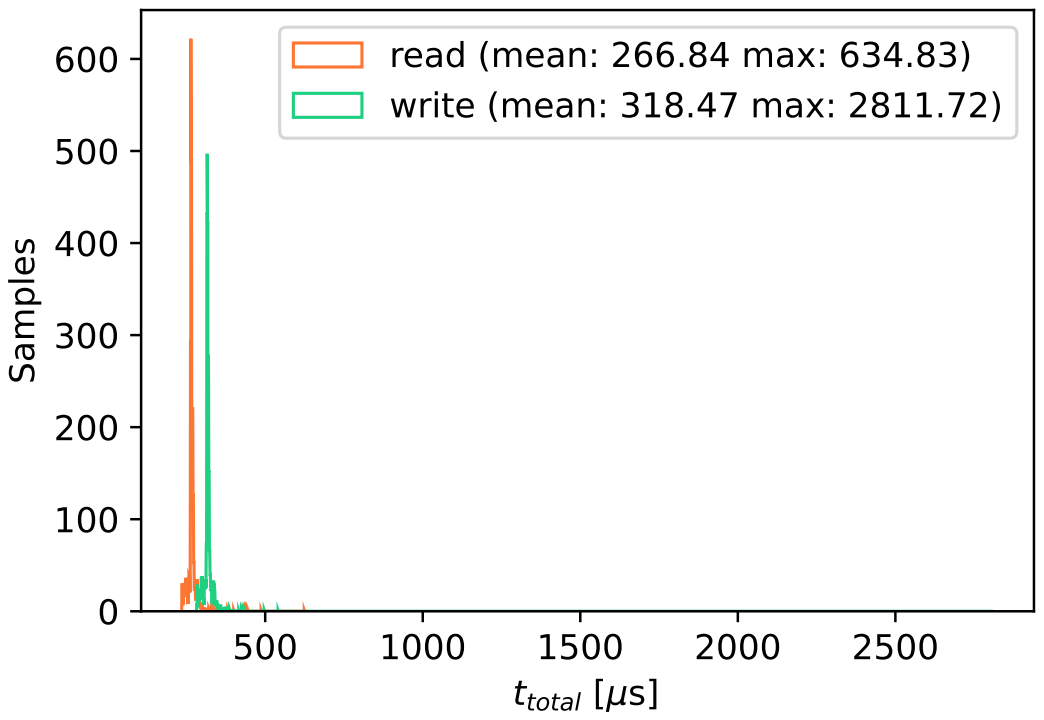
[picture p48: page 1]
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

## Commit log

2024-02-01 Add IK.py and FK.py from Raspberry folder
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2024-02-06 Track large files with Git LFS
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2025-03-28 2 joint test, event based
2025-03-28 Test with 2 joints
2025-03-31 check stall
2025-03-31 rework to include response flags on I2C transaction
2025-04-06 homeing call, still missing offset and gear ratio
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2025-04-07 Joint gear Ratio and bias
2025-04-07 busy flag and file reorg
    [configuration.h]
2025-04-09 arduino: home params
    [configuration.h]
2025-04-16 Arduino: parametrized encoder homing
2025-04-16 gitignore and encoder homeing
2025-04-16 Joint defines refined
    [configuration.h]
2025-04-17 Arduino: reset encoder on home
2025-04-28 Arduino: reduce Max velocity
    [configuration.h]
2025-04-28 I2C retries and some refinements
2025-04-28 WIP: Arduino: encoder stall
2025-04-28 Arduino: working stall detection via pid error
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2025-05-01 PWM test and 3joint test
2025-05-01 Arduino: fixed state setting
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2025-05-29 Updated Documentation
    [configuration.h]
2025-05-29 ranges, and PID error homing
2025-05-29 Aduino: PID error homing
2025-05-30 documents and documentation
    [J1_endstop.stl, J3_endstop_l.stl, J3_endstop_r.stl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]
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2025-09-22 Untrack files in .gitignore
    [base_link.stl, bioscara.xacro, bioscara_controllers.yaml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]
2025-09-24 max Accel and velocity implementation and test node
2025-09-25 tested max values
    [accel_test_10000000_200000.csv, accel_test_10000_200000.csv, accel_test_5000_10000.csv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]
2025-09-25 WIP: stall detection
2025-09-26 Improved Stall detection
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2025-09-29 hardware description: z height aligned
    [base_link.stl, bioscara.xacro, link_1_1.stl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]
2025-09-30 STOP: setRPM(0), with SP = PV joint goes back
2025-09-30 HW interface read i2c adress as base 16, basic ros control xacro
    [bioscara.xacro, bioscara_controllers.yaml]
2025-10-01 initial launch file
    [bioscara.urdf.xacro, bioscara.xacro]
2025-10-01 working launch with mock hardware and rqt trajectory gui
    [bioscara_controllers.yaml, bioscara_joint_trajectory_controller.yaml]
2025-10-03 tests with rqt_gui
    [bioscara_controllers.yaml]
2025-10-03 Fix URDF world frame
    [bioscara.urdf.xacro]
2025-10-06 change controller update rate
    [bioscara.urdf.xacro, bioscara_controllers.yaml]
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2025-10-09 test: use params from yaml
    [bioscara.urdf.xacro]
2025-10-09 config from yaml, urdf part
    [bioscara.urdf.xacro]
2025-10-09 fixed parsing issues
    [bioscara.urdf.xacro, bioscara_controllers.yaml]
2025-10-10 RT tests
    [accel_test_10000000_200000.csv, accel_test_10000_200000.csv, accel_test_5000_10000.csv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]
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2025-10-13 first stage tracking error tests
    [record_0p15707_1p5707_j1.csv]
2025-10-13 macro-fy description
    [bioscara.urdf.xacro, bioscara.xacro]
2025-10-13 second stage tracking error tests
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2025-10-14 add stepper tests
    [PID_error_test.csv, stepper_test.xlsx]
2025-10-14 remove stall prints
2025-10-14 initial velocity command interface
    [bioscara.xacro, bioscara_controllers.yaml]
2025-10-14 tracking error tests
    [bioscara_controllers.yaml, record_0p15707_0p157_j1_vel_p0p0_i0p0_d0p0_kff1p0_CM.csv, record_0p15707_0p157_j1_vel_p0p0_i0p0_d0p0_kff1p0_JTC.csv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]
2025-10-15 fix/stall no longer prevents activation, to be able to clear stall
2025-10-15 fix/set init commands to current position or 0 velocity
2025-10-15 WIP: high speed stall detection
2025-10-15 fix/reset i2c handle after deinit
2025-10-15 increase speeds and accel
    [bioscara_controllers.yaml]
2025-10-15 fixed export
    [record_0p314_0p157_j1_vel_p0p0_i0p0_d0p0_kff1p0.csv, record_0p314_0p157_j1_vel_p0p5_i0p0_d0p0_kff1p0.csv, record_0p314_1p57_j1_vel_p0p5_i0p0_d0p0_kff1p0.csv]
2025-10-22 wip: gripper
    [bioscara.urdf.xacro, bioscara.xacro, bioscara_arm.xacro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]
2025-10-22 start with hardware and controllers "inactive"
    [bioscara_controllers.yaml]
2025-10-22 allow read when not homed
    [bioscara_controllers.yaml]
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2025-10-24 change from offset to min/max
    [bioscara.urdf.xacro]
2025-10-24 always add position and velocity CIF
    [bioscara.xacro]
2025-10-24 wip: homing gpio controller
    [bioscara_controllers.yaml]
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2025-10-30 feat: homing controller, basic implemetation
    [bioscara_controllers.yaml, homing_controller_parameters.yaml]
2025-10-31 wip (untested): generalized singletrigger controller
    [bioscara_controllers.yaml, single_trigger_controller_parameters.yaml]
2025-11-01 feat: base and derived classes for hardware and mock joint
2025-11-01 homing controller fixes
    [bioscara_controllers.yaml, single_trigger_controller_parameters.yaml]
2025-11-01 fix: small make paramters work
    [bioscara_controllers.yaml, single_trigger_controller_parameters.yaml]
2025-11-01 fix: set initial flags and move mock homing logic to isHomed()
2025-11-01 fix: reset command to 0.0 when done homing
2025-11-03 fix: switch stop and postHoming
2025-11-03 feat: home as part of joint CIF and SIF
    [bioscara_controllers.yaml]
2025-11-03 fix: set offset before converting velocity to motor units
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2025-11-04 feat: generalize gripper classes
    [bioscara.xacro]
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2025-11-06 fix: use Gripper instead of MockGripper
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2025-11-10 wip: restructure gripper
    [bioscara.urdf.xacro, bioscara.xacro, bioscara_arm.xacro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]
2025-11-10 remove single_trigger_controller
    [single_trigger_controller_parameters.yaml]
2025-11-12 fix: remove joint name
2025-11-12 test: joint kinematic limits
    [j1_1.csv, j1_2.csv, j1_3.csv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]
2025-11-12 wip: SG_VALUE as stall criteria
2025-11-12 wip: highspeed stall
2025-11-13 wip: LUT stall threshold
    [configuration.h]
2025-11-13 feat: gripper HW IF works
    [bioscara_gripper_128.ros2_control.xacro, bioscara_gripper_128.urdf.xacro, bioscara_gripper_controllers.yaml]
2025-11-13 feat: package launch files
    [bioscara.urdf.xacro, bioscara_arm.xacro, robot.xacro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]
2025-11-13 feat: gripper meshes
    [base.stl, left_jaw.stl, materials.xacro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]
2025-11-14 fix: reset max velocity after homing
2025-11-14 fix: set and reset maxVelocity for homing
2025-11-14 feat: two regime stall threshold and tests
    [J3_DOWN_ramp.csv, J3_UP_ramp.csv, configuration.h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]
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2025-11-14 increase J2 Stall threshold
2025-11-14 doc: hint for stallguard
2025-11-15 feat: split CM and CTR parameter files
    [bioscara_gripper_controller_manager.yaml, bioscara_gripper_controllers.yaml]
2025-11-15 feat: split arm CM and CTR parameter files
    [bioscara_controller_manager.yaml, bioscara_controllers.yaml]
2025-11-16 feat: complete launch files in bringup and description packages
    [robot.xacro, scene.xacro]
2025-11-16 feat: package restructuring, split gripper and arm
    [base_link.stl, bioscara.urdf.xacro, bioscara_arm.xacro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]
2025-11-16 fix: rename dalsa_bioscara to dalsa_bioscara_arm
    [base_link.stl, bioscara.urdf.xacro, bioscara_arm.xacro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]
2025-11-18 feat: reject controller switch to velocity or position if joint not homed. Fixes #9.
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2025-11-19 change return type to driver error type
2025-11-19 feat: only have currently homed joint active. Closes #11 and # 12
2025-11-19 fix: start async timer
2025-11-20 fix: correct urdf names and package names
    [bioscara_arm.xacro, bioscara_gripper_128.xacro, scene.xacro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]
2025-11-20 feat: inital moveit config
    [joint_limits.yaml]
2025-11-21 fix: CSV header
    [j4_adaptive_stall_threshold_two_levels.csv]
2025-11-25 feat: make SETUP non-blocking. Fixes #18.
    [configuration.h]
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2025-11-25 fix: reset drive current on disable
2025-11-25 fix: reset values when homing is cancled
2025-11-25 feat: only enable stallguard if threshold > 0
2025-11-25 apply max limits
    [joint_limits.yaml]
2025-11-26 fix: call checkOrientation in setup. Fixes #20.
    Moved all setup work that is only done once in the program lifetime to arduino setup().
    Reason was issue #20, by reversing the coil connection the stepper could go wild on activation if the
    control threshold is exceeded. Because this USUALLY is not the case this bug has not been noticed.
2025-11-26 fix: make stall detection less sensitive
    decrease spike rejection threshold and increase LP filter time constant.
    Should make the overall error value lower and slower, decreasing the chance of false positive.
    Low speed detection will suffer.
2025-11-27 feat: reenable stall detection and disable loop animation in Rviz
2025-11-27 add pilz PTP joint limit problems
2025-11-27 Add RW_test data and README
    [100kHz.CSV, 400kHz.CSV, baseline.csv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]
2025-11-27 change author name
    [configuration.h]
2025-11-27 RW_test plots
    [position_100kHz.csv, position_400kHz.csv]
2025-11-27 doc: RW_test
    [velocity_100kHz.csv, velocity_400kHz.csv]
2025-12-06 fix: mimic joint limits
    [bioscara_gripper_128.urdf.xacro]
2025-12-06 feat: set gripper init_pos (#24)
    [bioscara_gripper_128.ros2_control.xacro]
2025-12-08 fix: correct tool_flange z-height (#27)
    [bioscara.urdf.xacro]
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2025-12-15 fix: add allow_nonzero_velocity_at_trajectory_end: true othewise execution errors
    [bioscara_arm_controllers.yaml]
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2025-12-16 rename dalsa_grippers -> dalsa_bioscara_grippers
    [base.stl, bioscara_gripper_128.ros2_control.xacro, bioscara_gripper_128.urdf.xacro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]
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
